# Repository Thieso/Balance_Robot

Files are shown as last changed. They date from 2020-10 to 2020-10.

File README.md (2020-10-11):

# Balance Robot

Balance Robot controlled using an Arduino Due. 

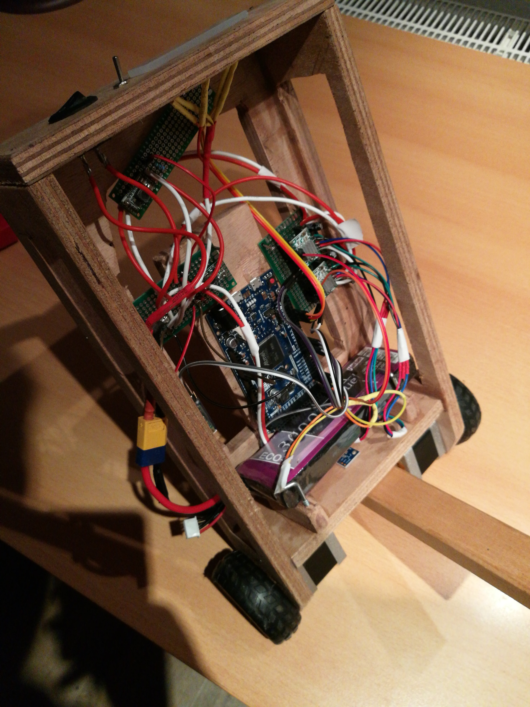
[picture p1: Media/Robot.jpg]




## Hardware

For the Hardware, an Arduino Due is used as a microcontroller. The Due has
higher performance than the typical Uno/Nano which is needed to drive the
motors.

The Arduino reads the sensor data from an MPU-9250 to get the angle of the robot
and then computes a PID control signal which is send to the  A4988 motor
controllers. The A4988 motor controllers deliver the appropriate amount of
current to the motors. To make the motors more quiet and more precise,
microstepping is used. There is a tradeoff between motor performance and
stepsize. Smaller steps require more computational power which the Arduino might
not be able to deliver. In this case quarter steps are used. 

The LEDs give feedback about the current angle of the robot. The middle LED
indicates the angle when the robot is upright. 

The power is provided by a 3 Cell Lipo. This is connected directly to the A4988
controllers as motor voltage input. For the Arduino the voltage is reduced
using a DC-DC converter to about 7-12V. 
The MPU-9250 sensor is powered by a 3.3V DC-DC converter output which also power
the internal logic of the A4988 controllers. 

The wiring is shown in the following picture. 

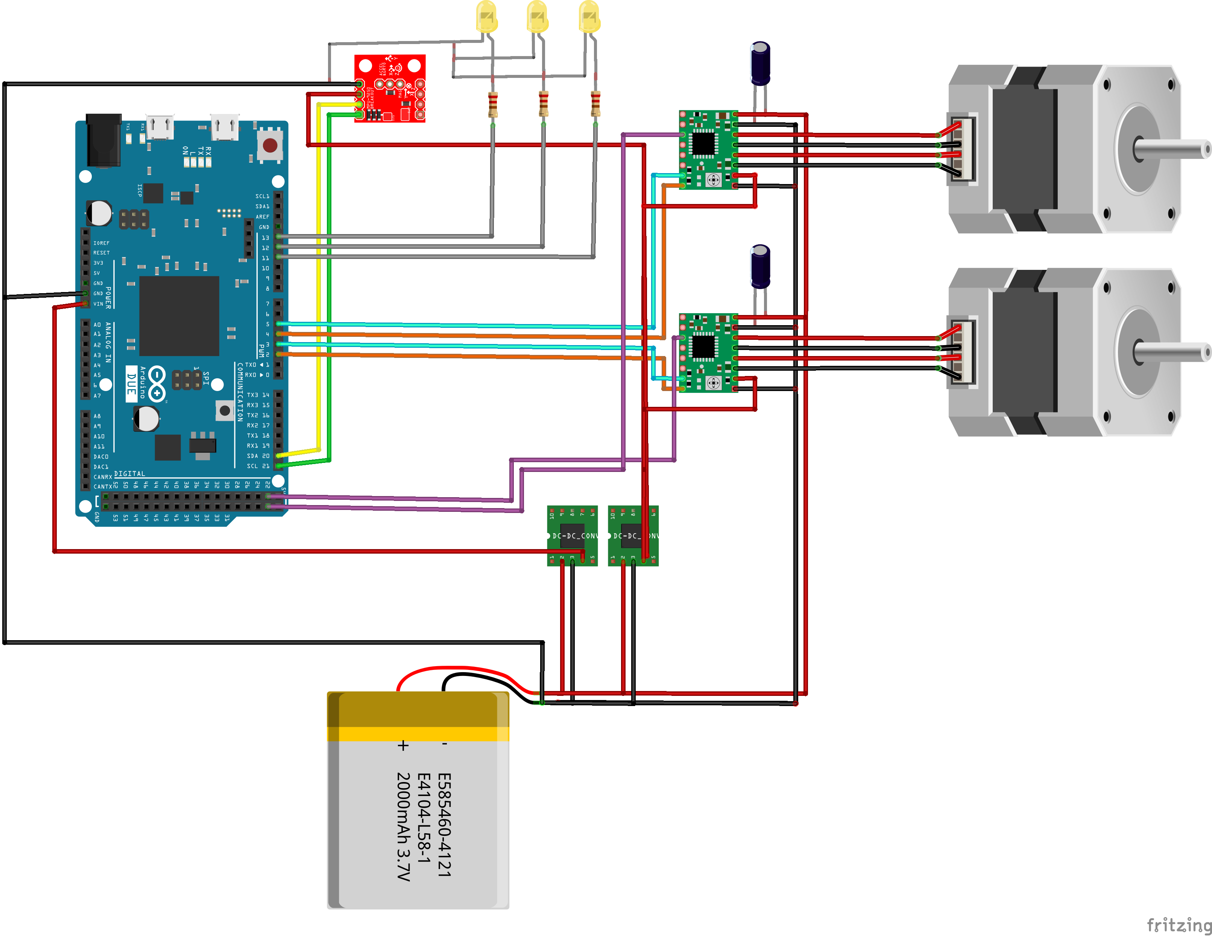
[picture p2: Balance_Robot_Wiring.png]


## Software

The control is done using simple PID control. An [PID
library](https://github.com/br3ttb/Arduino-PID-Library) can be found on github.
The output of the PID controller sets the speed of the motor. Important is that
the motors are accelerated to the desired speed in a smooth fashion. This
achieves a smoother motion and also makes sure the motors do not block when the
instantaneous acceleration is too high. In order to enable acceleration, the
[Accel Stepper](https://www.airspayce.com/mikem/arduino/AccelStepper/) library
is used for the motor control. 

In order to obtain the angle from the MPU-9250 breakout, the
[MPU9250](https://github.com/hideakitai/MPU9250) library is used. It provides an
easy interface with the sensor. In my case, the sensor data was very noisy, this
can lead to problems with the control. Therefore, the obtained angle is low pass
filtered before used in the controller. The low pass filter code can be obtained
from
[this](http://www.schwietering.com/jayduino/filtuino/index.php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`)
website.

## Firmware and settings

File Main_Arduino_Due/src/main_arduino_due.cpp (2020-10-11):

// include relevant libraries
#include <Arduino.h>
#include <Wire.h>
#include <PID_v1.h>
#include <SparkFunMPU9250-DMP.h>
#include <AccelStepper.h>
#include <MultiStepper.h>
//#include "eeprom_utils.h"

// max angle to show on LEDs
#define MAX_ANGLE 16
#define LED_ANGLE 5

// Define maximum motor speed
#define MAX_SPEED 2000

// define controller sample rate [ms]
#define CONTROLLER_SAMPLE_RATE 10

// LED pins
#define LED_PIN_1  11
#define LED_PIN_2  12
#define LED_PIN_3  13

// Define pin connections
#define DIR_PIN_R 2
#define STEP_PIN_R 3
#define DIR_PIN_L 4
#define STEP_PIN_L 5
#define MS1_L 22
#define MS2_L 24
#define MS3_L 26
#define MS1_R 23
#define MS2_R 25
#define MS3_R 27


// define controller parameters
// velocity controller
const double Kp_v = 0;
const double Kd_v = 0;
const double Ki_v = 0;
// angle controller
const double Kp_a = 380;
const double Kd_a = 30;
const double Ki_a = 5;
// angle variable
double current_angle = 0;
// setpoint
double sp = 0;
// control signals
double u_v = 0;
double u_a = 0;
int u_a_send = 0;
// bytes for SPI comms
byte bytesToSend[2];
byte b1, b2;
//current speed of vehicle
int speed_read = 0;

// time variables
long current_time, elapsed_time, prev_time = 0;

// define PID controller objects
PID PID_angle(&current_angle, &u_a, &sp, Kp_a, Ki_a, Kd_a, DIRECT);

// create sensor object
MPU9250_DMP imu;

// Define motor interface type
#define motorInterfaceType 1

// Creates an instance of the stepper motor class
AccelStepper left_motor(motorInterfaceType, STEP_PIN_L, DIR_PIN_L);
AccelStepper right_motor(motorInterfaceType, STEP_PIN_R, DIR_PIN_R);
MultiStepper steppers;

// positions of the motors
long positions[2];

// helper function to set microstep size
void setMicrosteps(int motor, int ms1, int ms2, int ms3) {
    if (motor == 0) {
        digitalWrite(MS1_L, ms1);
    } else {
        digitalWrite(MS1_R, ms1);
    }
}

class FilterBuLp1
{
    public:
        FilterBuLp1()
        {
            v[0]=v[1]=0.0;
        }
    private:
        float v[2];
    public:
        float step(float x) //class II 
        {
            v[0] = v[1];
            v[1] = (8.636402701376222346e-2 * x)
                 + (0.82727194597247555308 * v[0]);
            return 
                 (v[0] + v[1]);
        }
};
// filter object
FilterBuLp1 filter;

// ================================================================
// ===                      INITIAL SETUP                       ===
// ================================================================

void setup() {
    Serial1.begin(9600);

    // setup LED pins as output and turn them on and off to see if they work
    pinMode(LED_PIN_1, OUTPUT);
    pinMode(LED_PIN_2, OUTPUT);
    pinMode(LED_PIN_3, OUTPUT);
    digitalWrite(LED_PIN_1, HIGH);
    digitalWrite(LED_PIN_2, HIGH);
    digitalWrite(LED_PIN_3, HIGH);
    delay(500);
    digitalWrite(LED_PIN_1, LOW);
    digitalWrite(LED_PIN_2, LOW);
    digitalWrite(LED_PIN_3, LOW);

    // Call imu.begin() to verify communication and initialize
    if (imu.begin() != INV_SUCCESS)
    {
        while (1)
        {
            //Serial.println("Unable to communicate with MPU-9250");
            //Serial.println("Check connections, and try again.");
            //Serial.println();
            delay(5000);
        }
    }

    imu.dmpBegin(DMP_FEATURE_6X_LP_QUAT | // Enable 6-axis quat
            DMP_FEATURE_GYRO_CAL, // Use gyro calibration
            1000/CONTROLLER_SAMPLE_RATE); // Set DMP FIFO rate in hz
    // DMP_FEATURE_LP_QUAT can also be used. It uses the 
    // accelerometer in low-power mode to estimate quat's.
    // DMP_FEATURE_LP_QUAT and 6X_LP_QUAT are mutually exclusive
    // setLPF() can be used to set the digital low-pass filter
    // of the accelerometer and gyroscope.
    // Can be any of the following: 188, 98, 42, 20, 10, 5
    // (values are in Hz).
    imu.setLPF(5); 

    // set PID sample time
    PID_angle.SetSampleTime(CONTROLLER_SAMPLE_RATE);
    // set PID output limits
    PID_angle.SetOutputLimits(-MAX_SPEED, MAX_SPEED);
    // start PID controllers
    PID_angle.SetMode(AUTOMATIC);

    // set microstepping for the motors
    pinMode(MS1_L, OUTPUT);
    pinMode(MS1_R, OUTPUT);
    setMicrosteps(0, HIGH, LOW, LOW);
    setMicrosteps(1, HIGH, LOW, LOW);

    // motor setup
    left_motor.setMaxSpeed(MAX_SPEED);
    //left_motor.setAcceleration(MAX_ACCELERATION);
    left_motor.setSpeed(0);
    right_motor.setMaxSpeed(MAX_SPEED);
    //right_motor.setAcceleration(MAX_ACCELERATION);
    right_motor.setSpeed(0);

    steppers.addStepper(left_motor);
    steppers.addStepper(right_motor);
}



// ================================================================
// ===                    MAIN PROGRAM LOOP                     ===
// ================================================================

void loop() {
    //Serial.println(millis());
    // Check for new data in the FIFO
    if ( imu.fifoAvailable() )
    {
        // Use dmpUpdateFifo to update the ax, gx, mx, etc. values
        if ( imu.dmpUpdateFifo() == INV_SUCCESS)
        {
            // computeEulerAngles can be used -- after updating the
            // quaternion values -- to estimate roll, pitch, and yaw
            imu.computeEulerAngles();
        }
        // get the current angle 
        if (imu.roll > 300) {
            current_angle = 360 - imu.roll;
        } else {
            current_angle = - imu.roll;
        }

        // compute new controller value
        PID_angle.Compute();
        u_a = filter.step(u_a);
        Serial1.println(u_a);

        // set motor spinning direction for the steppers
        if (u_a > 0) {
            positions[0] = -10000;
            positions[1] = 10000;
        } else {
            positions[0] = 10000;
            positions[1] = -10000;
        }
        left_motor.setMaxSpeed(u_a);
        right_motor.setMaxSpeed(u_a);
        steppers.moveTo(positions);
        //
        // set LEDs based on the angle
        analogWrite(LED_PIN_1, min(255, max(0, current_angle / LED_ANGLE * 255)));
        analogWrite(LED_PIN_2, max(0, 255 - abs(current_angle) / LED_ANGLE * 255));
        analogWrite(LED_PIN_3, min(255, max(0, -current_angle / LED_ANGLE * 255)));
    }

    // run the motors
    steppers.run();
}

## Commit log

2020-09-27 Added picture and video of robot. Added fritzing wiring file. Adapted README to incorparate the new media
    [Balance_Robot_Wiring.fzz]
2020-09-28 Changed from SPI to I2C communications, implemented bluetooth module to send data wirelessly
2020-10-11 Changed setup from two Arduinos to one Arduino Due Adapted wiring diagram Adapted the code to run fully on only the Due deleted code of the other Arduinos
    [Balance_Robot_Wiring.fzz]
2020-10-11 Changed picture and gif to resemble the new robot config with only the Arduino Due and much better balancing
